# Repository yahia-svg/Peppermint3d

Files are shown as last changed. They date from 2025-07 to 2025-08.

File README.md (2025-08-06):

# Peppermint3d
This is my fully custom designed bed slinger. I tried to make it as structurally sound as possible, by using mostly metal components like the opengantry universal plate and a ridgid aluminum frame, whilst still being fairly simple so i'd be able to build it as a beginner
# Motivation
I made this project because I was completely new to designing 3d printers and I thought this would be a great first printer. Additionally, this would help me so much with developing other hardware projects because the 3d printing service that I use is slow and expensive.
# Design
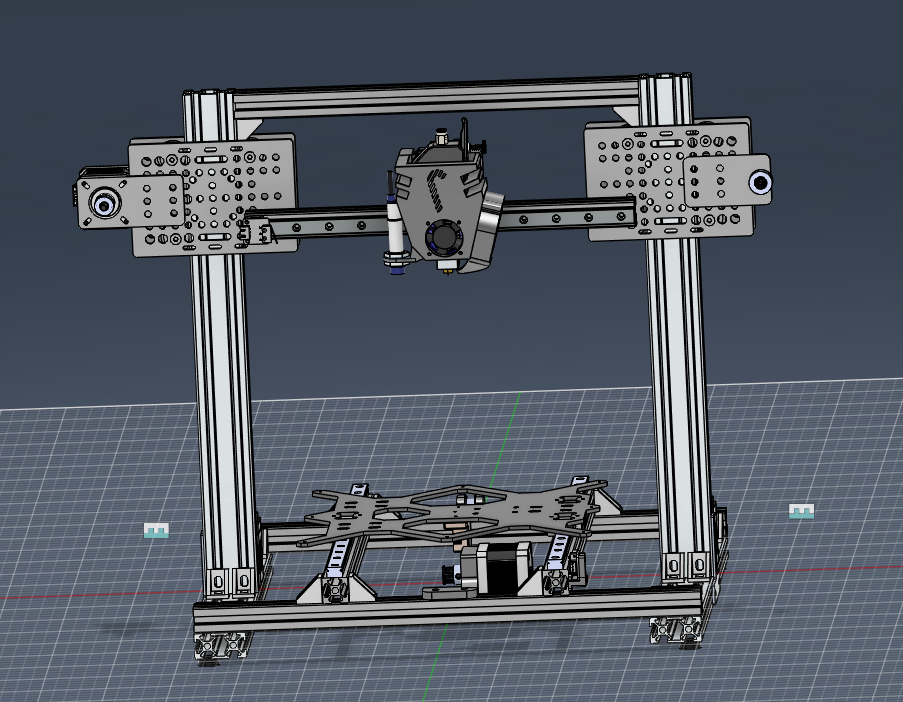
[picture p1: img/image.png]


# Video(Click to Play)
video (https://youtu.be/M26KKw5ZoOQ)

# BOM
| QUANTITY | NAME | COST | LINK | Notes |
|---|---|---|---|---|
| 1 | BIGTREETECH SKR MINI E3 V3.0 32 Bit Control Board | £3,300.00  | https://fluxelectronix.com/shop/bigtreetech-skr-mini-e3-v3-0-32-bit-control-board/ | |
| 1 | Proximity-Sensor | £140.00 | https://ampere-electronics.com/product/lj12a3-4-z-proximity-sensor-pnp-12mm-dia-4mm-3-wire-dc6-36v/ | |
| 1 | Raspberry Pi Zero 2 W | £0.00 | https://www.ram-e-shop.com/ar/shop/raspberry-pi-zero-2w-raspberry-pi-zero-2-w-9256 | will pay from terminal craft grant |
| 1 | ADXL345 Digital Accelerometer | £190.00 | https://ampere-electronics.com/product/gy-291-adxl345-accelerometer-module/ | |
| 1 | 5015 Blower fan -- 24v | £60.00 | https://fluxelectronix.com/shop/5015-blower-fan-12vdc/ | |
| 1 | E3d V6 Hotend full kit | £325.00 | https://fluxelectronix.com/shop/e3d-v6-j-head-hotend-1-75mm-extruder-nozzle-0-4mm/ | |
| 1 | Aluminium headted(214mm*214mm) 24v | £290.00 | https://fluxelectronix.com/shop/3d-printer-mk3-aluminum-heatbed-214x214x3mm-dual-supply/ | |
| 1 | Power Supply SMPS 240W 24V / 10A | £540.00 | https://fluxelectronix.com/shop/power-supply-smps-240w-24v-10a/ | |
| 1 | AC Inlet power socket with fuse holder | £15.00 | https://fluxelectronix.com/shop/panel-mount-ac-inlet-power-socket-with-fuse/ | |
| 1 | Power Supply cable | £35.00 | https://fluxelectronix.com/shop/ac-power-cord-with-iec-c13-connector/ | |
| 1 | zip ties | £25.00 | https://fluxelectronix.com/shop/200mm-nylon-cable-ties-pack-of-100-pcs-china/ | |
| 1 | NTC 100K ohm thermistor for heated bed | £30.00 | https://fluxelectronix.com/shop/100k-ohm-ntc-thermistors-temperature-sensor-with-cable-for-3d-printer-2pin-dupont-head/ | |
| 1 | Anti-vibration Rubber Feet, 4Pcs | £60.00 | https://fluxelectronix.com/shop/anti-vibration-rubber-feet-4pcs/ | |
| 4 | stepper Motor (NEMA-17) 17HS4401 | £1,600.00  | https://ampere-electronics.com/product/nema17-stepper-motor-17hs4401s-38mm/ | |
| 1 | Nema17 Stepper Motor 17HS4023 – 23mm | £315.00 | https://fluxelectronix.com/shop/nema17-stepper-motor-17hs4023-23mm/ | |
| 2 | Creality Ender-3/PRO Endstop Switch Module | £110.00 | https://fluxelectronix.com/shop/creality-ender-3-pro-endstop-switch-module/ | |
| 1 | Aluminium headted(214mm*214mm) 24v | £290.00 | https://fluxelectronix.com/shop/3d-printer-mk3-aluminum-heatbed-214x214x3mm-dual-supply/ | |
| 1 | PEI Sheet Double Side Textured Smooth 220x220mm | £900.00 | https://fluxelectronix.com/shop/pei-sheet-textured-smooth-220mm-twotrees/ | |
| 1 | bondtech bmg extruder kit | £475.00 | https://fluxelectronix.com/shop/flexible-consumables-double-gear-extruder-bondtech-bmg-reduced-extruder/ | |
| 1 | 32gb sd card for raspberry pi | £375.00 | https://www.ram-e-shop.com/ar/shop/micro-sd-32gb-krt-mymwry-mykrw-32-jyj-hc10-6298 | |
| 4 | Leveling Screw (M3*40) | £60.00 | https://fluxelectronix.com/shop/leveling-kit-m3-screw-spring-knob-for-3d-printer/ | |
| 1 | Heat Bed High Power MOSFET Module 25A | £160.00 | https://fluxelectronix.com/shop/heat-bed-high-power-mosfet-module-25a/ | |
| 1 | Electric Copper Wire (1.5mm, 16 AWG, 1 Meter) | £22.50 | https://ampere-electronics.com/product/electric-copper-wire-1-5mm-16-awg-1-meter-el-sewedy-electric/ | |
| 3 | AWG22 copper wire | £15.00 | https://fluxelectronix.com/shop/copper-wire-0-5mm-22awg-1meter-long/ | |
| 1 | Dupont Crimp Connector Kit – 310Pcs | £135.00 | https://fluxeelectronix.com/shop/dupont-crimp-connector-kit-310pcs/ | |
| 4 | openbuilds universal gantry plate | £660.00 | https://fluxelectronix.com/shop/steel-v-slot-universal-gantry-plate-openbuilds/ | |
| 1 | PRUSA Y-carriage Plate | £200.00 | https://fluxelectronix.com/shop/prusa-y-carriage-plate-for-214x214mm-heated-bed-plate-black-steel/ | |
| 2 | Steel Flat T-Joining Plate | £90.00 | https://fluxelectronix.com/shop/steel-flat-t-joining-plate/ | |
| 1 | Steel Nema17 Motor Mount Plate | £45.00 | https://fluxelectronix.com/shop/steel-nema17-motor-mount-plate-openbuilds/ | |
| 1 | Steel Idler Pulley Plate | £40.00 | https://fluxelectronix.com/shop/steel-idler-pulley-plate-openbuilds/ | |
| 2 | Anti-Backlash Nut Block | £140.00 | https://fluxelectronix.com/shop/tr8x8-anti-backlash-nut-block-for-acme-lead-screw/ | |
| 2 | TR8x8 Acme Lead Screw – 300mm | £190.00 | https://fluxelectronix.com/shop/tr8x8-acme-lead-screw-300mm/ | |
| 2 | 5x8MM Flexible Shaft Coupler | £90.00 | https://fluxelectronix.com/shop/5x8mm-flexible-shaft-coupler/ | |
| 2 | Flange Bearing F688ZZ | £50.00 | https://ampere-electronics.com/product/f688zz-miniature-flanged-ball-bearing-8x16x5mm/ | |
| 8 | v wheel | £360.00 | https://fluxelectronix.com/shop/delrin-v-wheel/ | |
| 2 | toothless idler pulley | £70.00 | https://fluxelectronix.com/shop/toothless-gt2-idler-pulley-5mm-bore/ | |
| 2 | 20Teeth GT2 Timing Belt Pulley, 6mm Width, 5mm Bore | £60.00 | https://fluxelectronix.com/shop/20teeth-gt2-timing-belt-pulley-5mm-bore/ | |
| 21 | Aluminum Profile Corner Bracket | £273.00 | https://ampere-electronics.com/product/2020-aluminum-profile-corner-bracket/ | |
| 2 | 1m gt2 6mm belt | £90.00 | https://ampere-electronics.com/product/gt2-open-belt-6mm-wide-pu-with-steel-core-1-meter-black/ | |
| 9 | 6mm m5 spacer | £45.00 | https://fluxelectronix.com/shop/aluminum-spacer-5-1x10x6mm/ | |
| 1 | 1 meter mgn12 linear rail | £1,300.00  | https://ampere-electronics.com/product/mgn12-linear-rail-guide-1000mm/ | I will cut it up into 350mm 300mm and 300mm |
| 4 | mgn12 linear rail carriage | £2,000.00  | https://fluxelectronix.com/shop/mgn12h-linear-bearing-block/ | |
| 2.5 | v slot aluminum extrusion 2020 | £462.00 | https://fluxelectronix.com/shop/2020-v-slot-aluminum-profile-extrusion-1m-black-anodized/ | |
| 2 | v slot aluminum extrusion 2040 | £600.00 | https://fluxelectronix.com/shop/2040-v-slot-aluminum-profile-extrusion-1m-black-anodized/ | |
| 1 | 10 pack m5 washer | £6.00 | https://fluxelectronix.com/shop/m5-flat-galvanized-steel-washer-pack-of-10/ | |
| 1 | 3d printing estimate(3egp per gram) | £480.00 | Printify3d | |
| 1 | delivery estimate | £300.00 | Delivery for Printify - Flux - Ampere | |
| 1 | Screws and T nuts | £0.00 | | Will buy from my own money because it won't fit in the grant |
| | TOTAL PRICE | £17,018.50 | | |
| | PRICE IN USD | £351.26 | | |

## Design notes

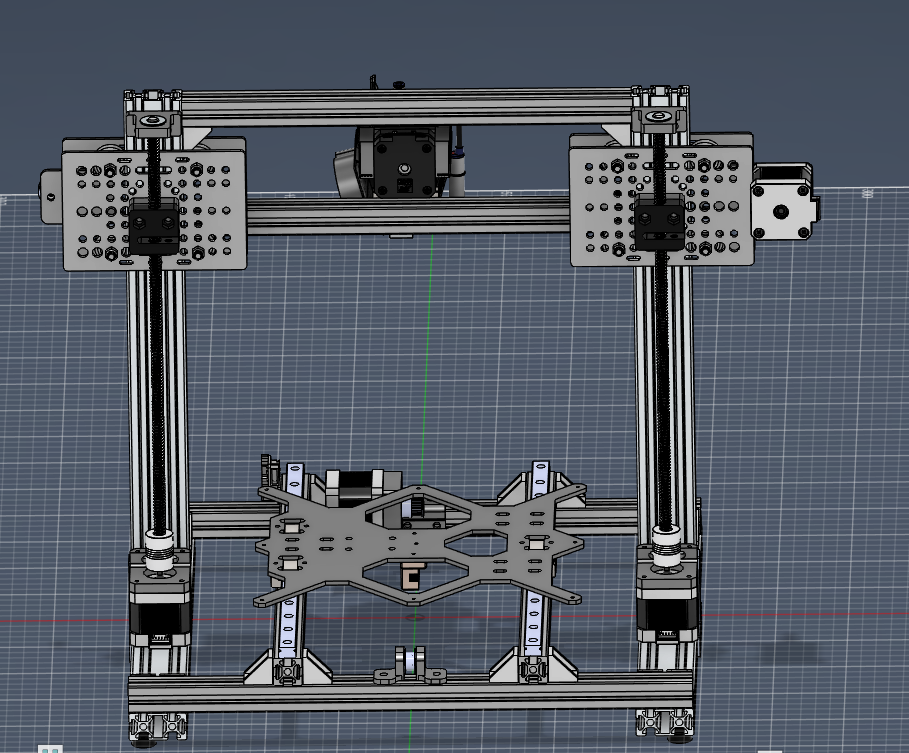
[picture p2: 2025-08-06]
img/Screenshot 2025-08-06 234610.png

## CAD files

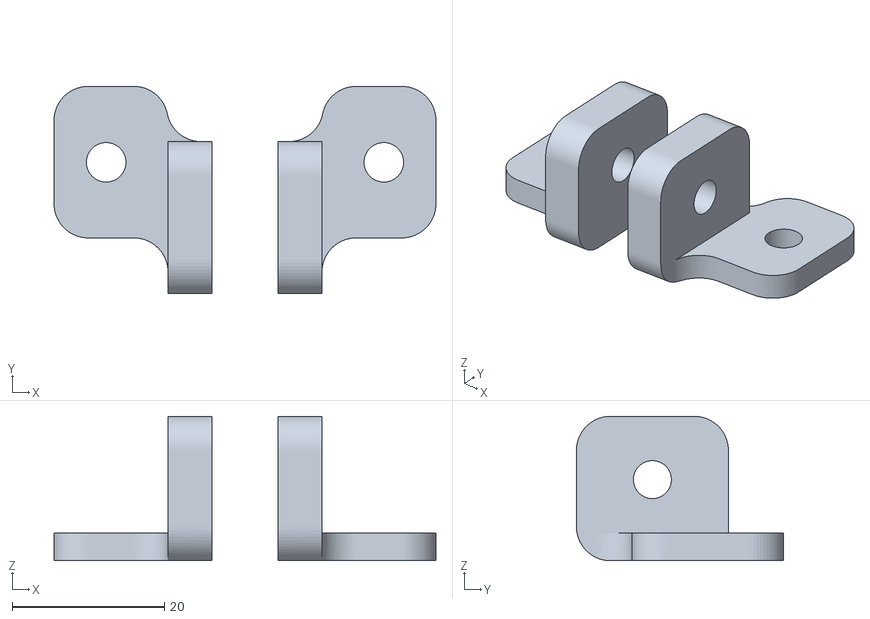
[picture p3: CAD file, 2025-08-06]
stl/idlerholder_y.stl
50.2 x 27.3 x 19.0

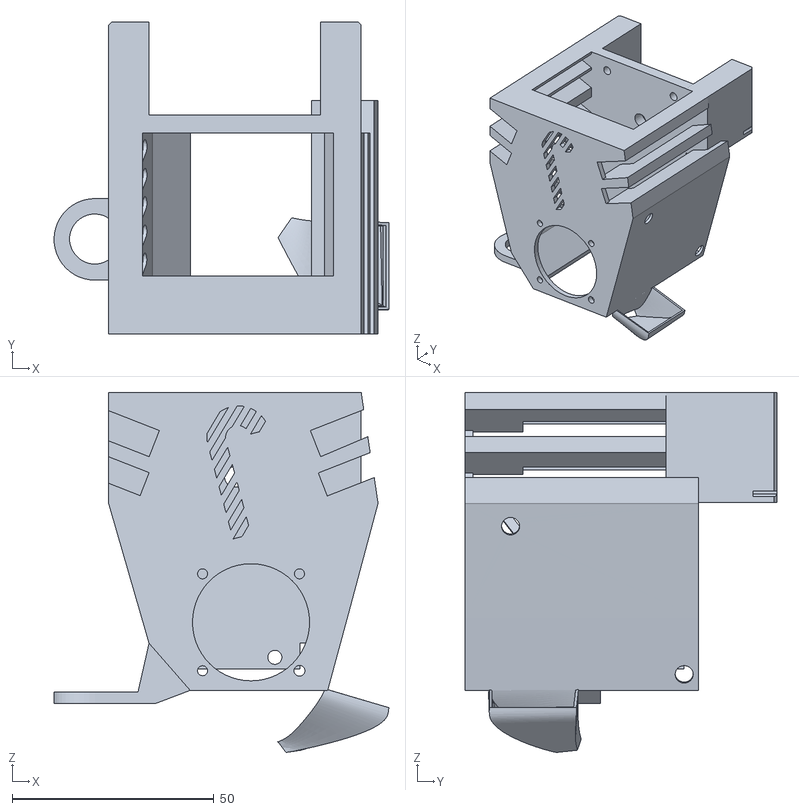
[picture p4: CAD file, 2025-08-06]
stl/printhead.stl
82.9 x 77.3 x 89.2

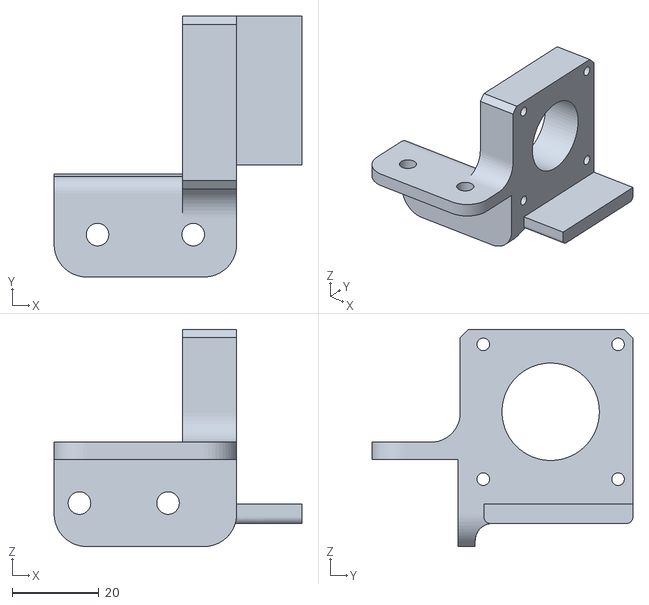
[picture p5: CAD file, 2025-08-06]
stl/motormount_y.stl
57.0 x 60.0 x 49.9

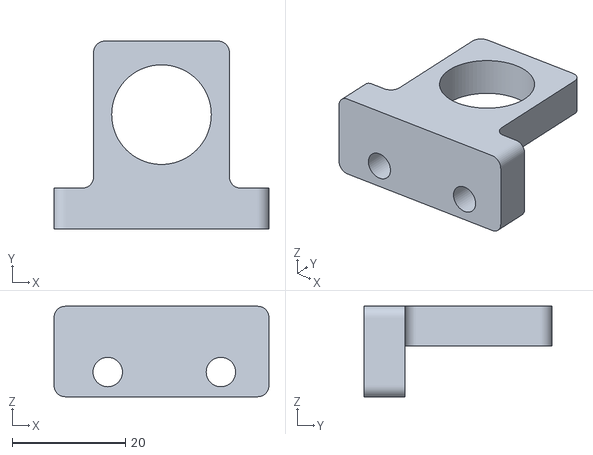
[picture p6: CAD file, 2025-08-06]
stl/bearingholder2_z .stl
38.0 x 33.2 x 16.0

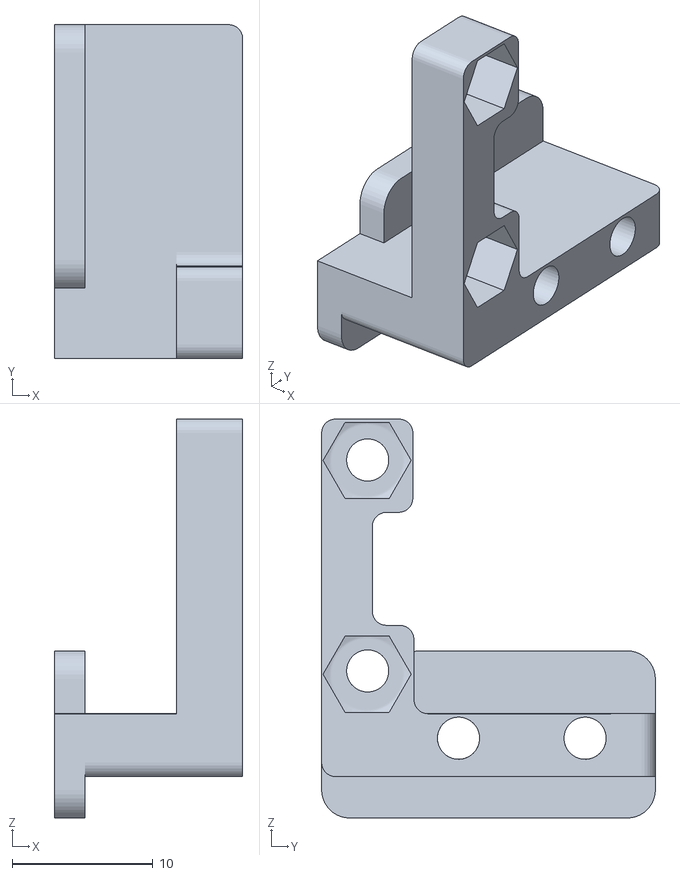
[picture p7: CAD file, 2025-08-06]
stl/endstop_y.stl
13.4 x 23.7 x 28.4

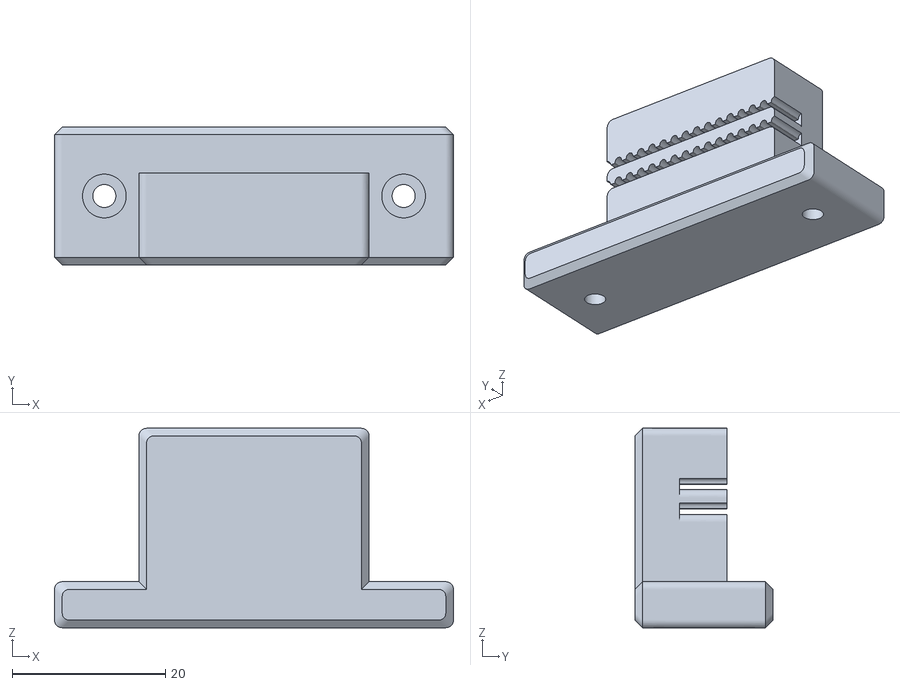
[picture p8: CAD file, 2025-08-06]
stl/MK3s_y_belt_holder_v1.0.stl
52.0 x 18.0 x 26.0

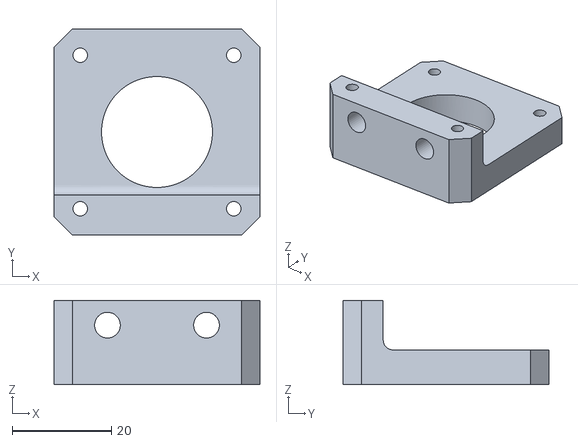
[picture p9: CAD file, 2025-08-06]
stl/motormount1_z.stl
41.6 x 41.6 x 17.0

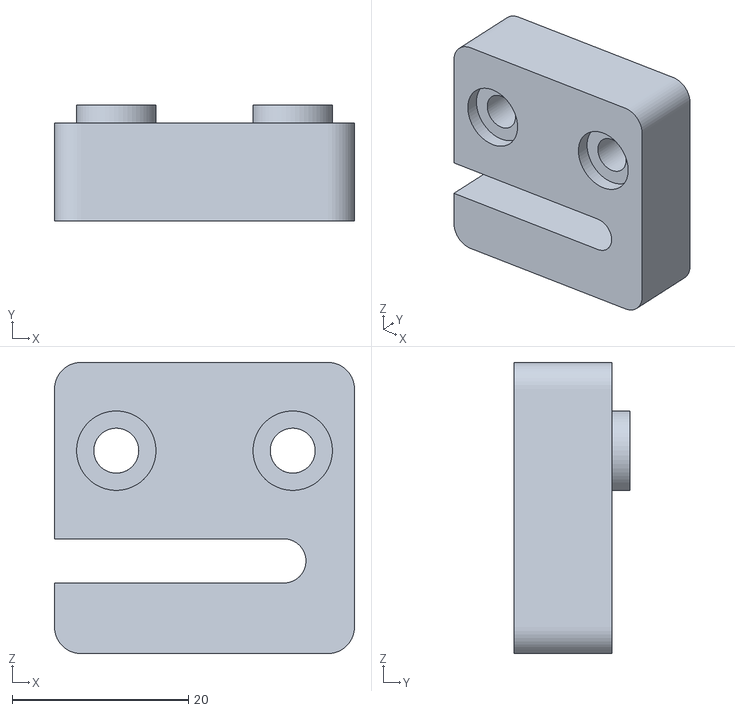
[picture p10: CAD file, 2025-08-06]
stl/antibacklashholder1_z.stl
34.0 x 13.1 x 33.0

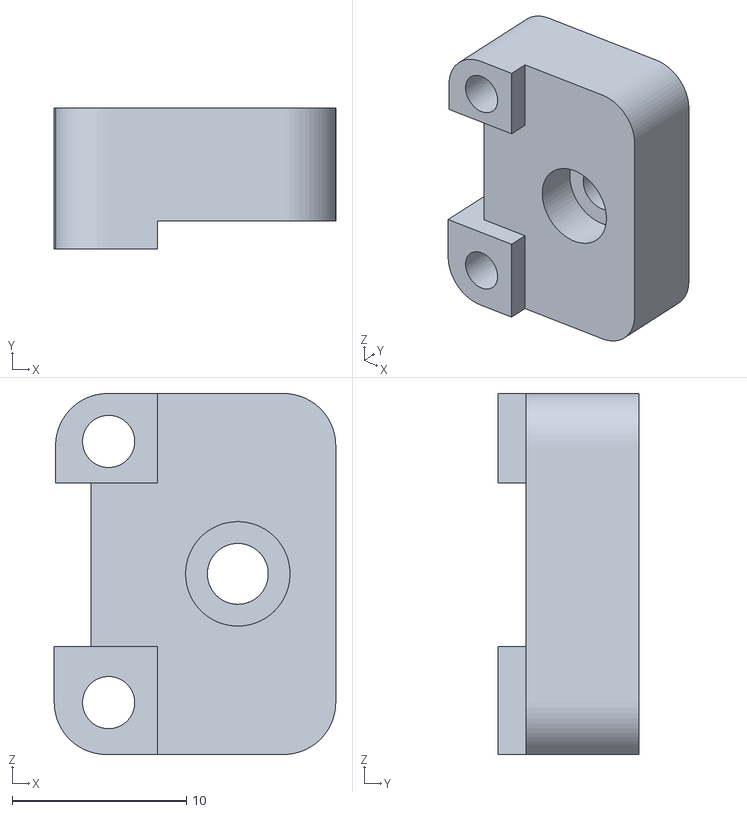
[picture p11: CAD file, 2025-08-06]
stl/endstop_x.stl
16.2 x 8.10 x 20.7

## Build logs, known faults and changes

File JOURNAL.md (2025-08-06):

## Total Hours: 19.5
| Key | Value |
|---|---|
| **Title** | Peppermint3d |
| **Author**  | Yahia Haggag |
| **Description** | My first custom bed slinger 3d printer designed to be sturdy and sleek |
| **Created At** | 2025-07-27 |

### 7/27/2025
As a complete noob to 3d printing and hardware I felt completely lost at first, so I started researching. I researched the different kinds of 3d printers and I finally settled on the bed slinger. I chose the bed slinger because it's a great choice for a first builds due to its simplicity and intuitive design. When choosing the specs for my printer I was focused on making it cheap and precise, therefore I've decided to use linear rails for the X and Y axis for precision and a lead screw actuator and v slot rails for the Z axis instead of linear rails to reduce costs. For the print head, I decided to use a direct drive bmg extruder to reduce stringing, and I coupled it with the e3d v6 volcano hotend, since it was really cheap and good enough for my needs, I also added a proximity sensor. For the print volume, I decided to go with 214*214*250 which is mostly sufficient for the things I print. To run this entire thing I decided to go with the BIGTREETECH SKR MINI E3 V3.0 board, because it's really cheap, really well docummented and runs klipper. I also estimated to cost to be 290USD based on local prices.
#### Time Elapsed: 7 Hrs 
### 7/28/2025
I hopped on fusion360 and got straight to designing I didn't do much as I was very unfimilliar with fusion but i managed to create a simple frame which I thought was strudy enough to support my 3d printer. I focused on strengthining my x axis by using 2040 extrusions and using a corner bracket and t plate combo because the x axis moves the most and it can be quite heavy
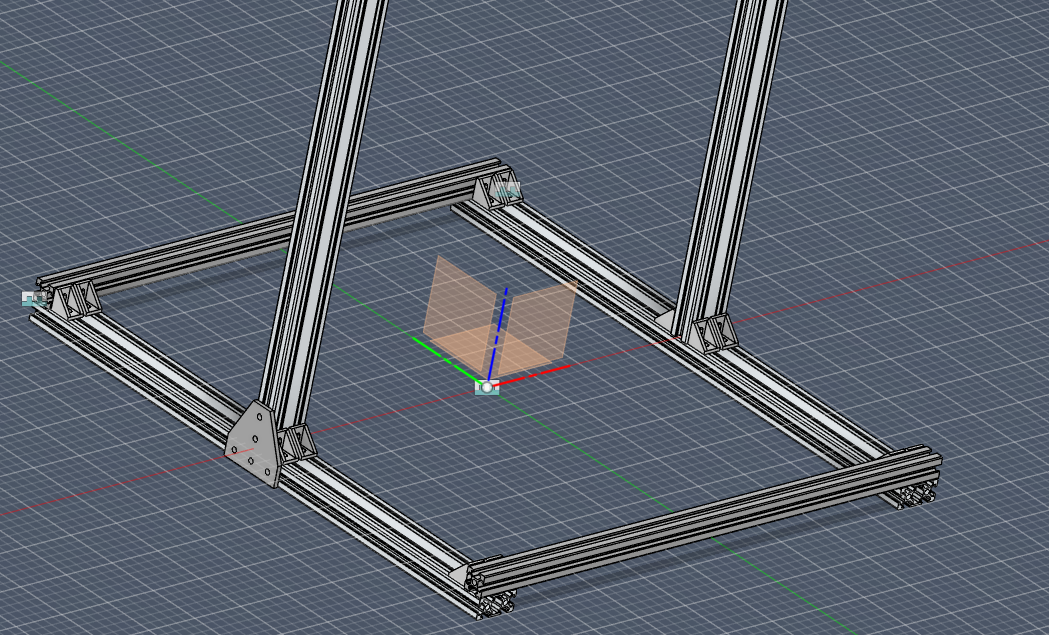
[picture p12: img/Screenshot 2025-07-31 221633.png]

#### Time Elapsed: 2 Hrs 
### 7/29/2025
I designed this endstop which is triggered by the linear rail carriage, this endstop helps me shorten the length of the linear rail as much as possible thus reducing cost. I also found out that the linear rail sizes I had initially calculated were incorrect, and now they're 350mm. I used the bed mount from the prusa mk3 since it was the only one available in my country that I could find the datasheet for online, and it also supports linear rails. So I had to use it since fabricating my own bed mount was going to be super expensive.
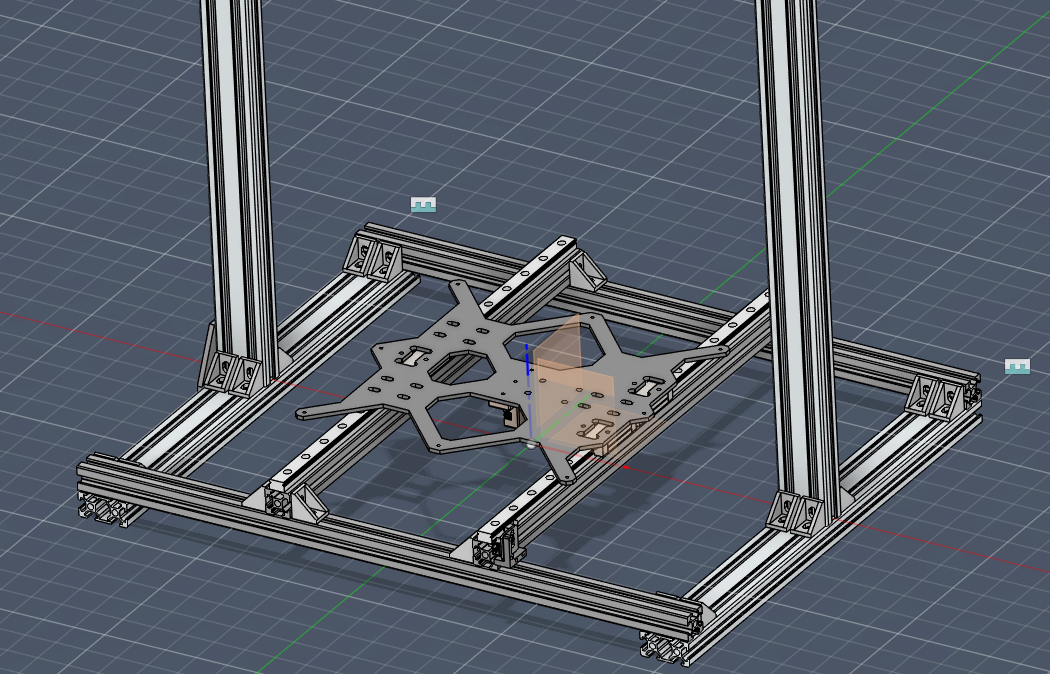
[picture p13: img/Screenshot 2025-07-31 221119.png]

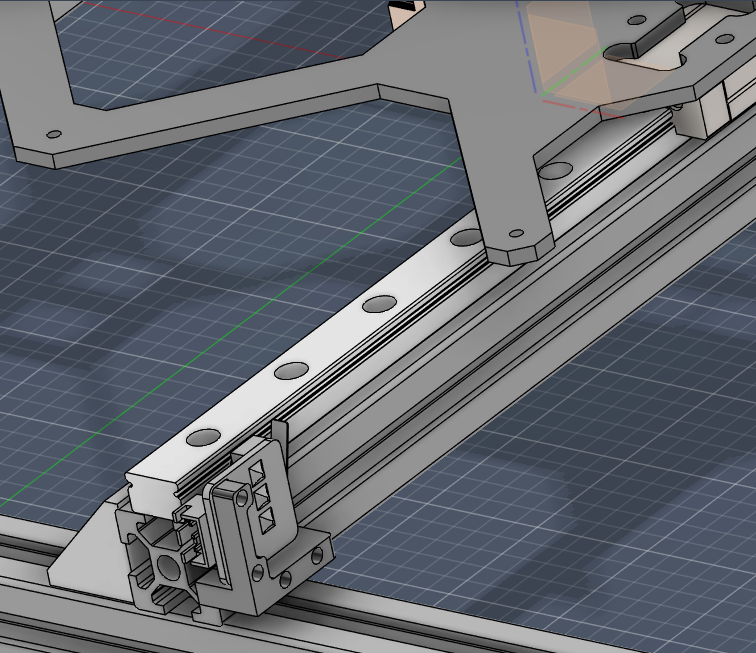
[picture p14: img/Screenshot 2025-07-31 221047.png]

#### Time Elapsed: 1.5 Hrs 
### 7/30/2025
Created a belt system for the y axis and added 4 anti vibration rubber feet
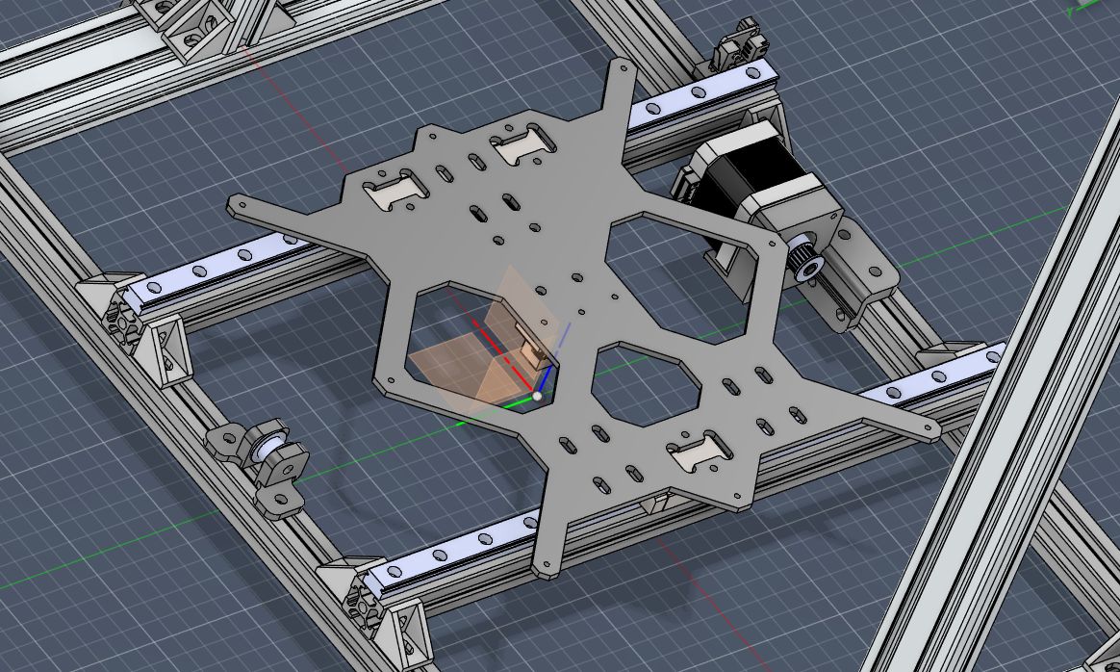
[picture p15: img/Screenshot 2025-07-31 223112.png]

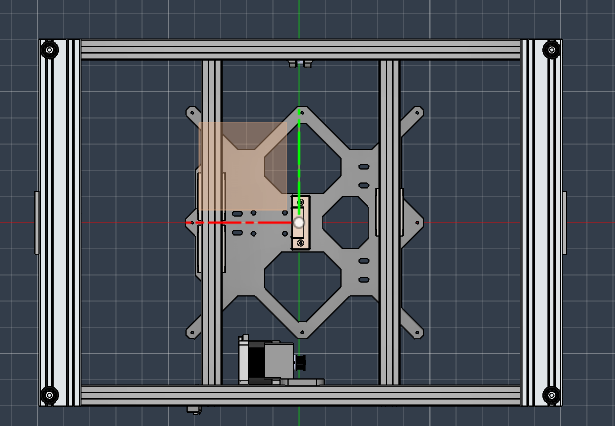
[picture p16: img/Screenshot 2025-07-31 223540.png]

#### Time Elapsed: 2 Hrs 
### 7/31/2025
I decided to lock in and I finished the entire z axis! I used openbuilds universal gantry plate because it's made of metal and has high surface area which means I can make the print head super heavy and I don't really have to worry.
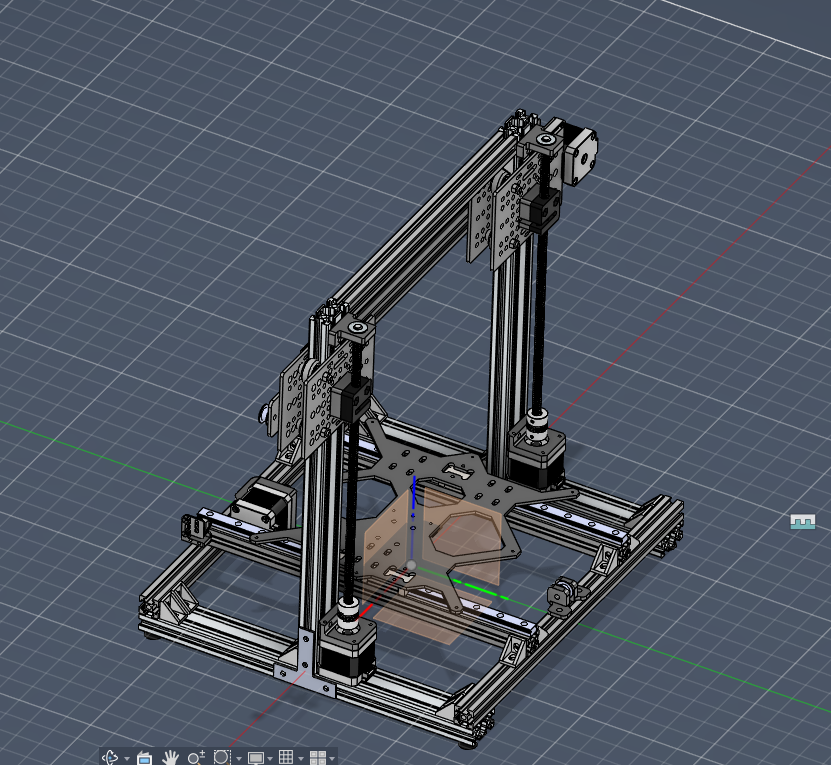
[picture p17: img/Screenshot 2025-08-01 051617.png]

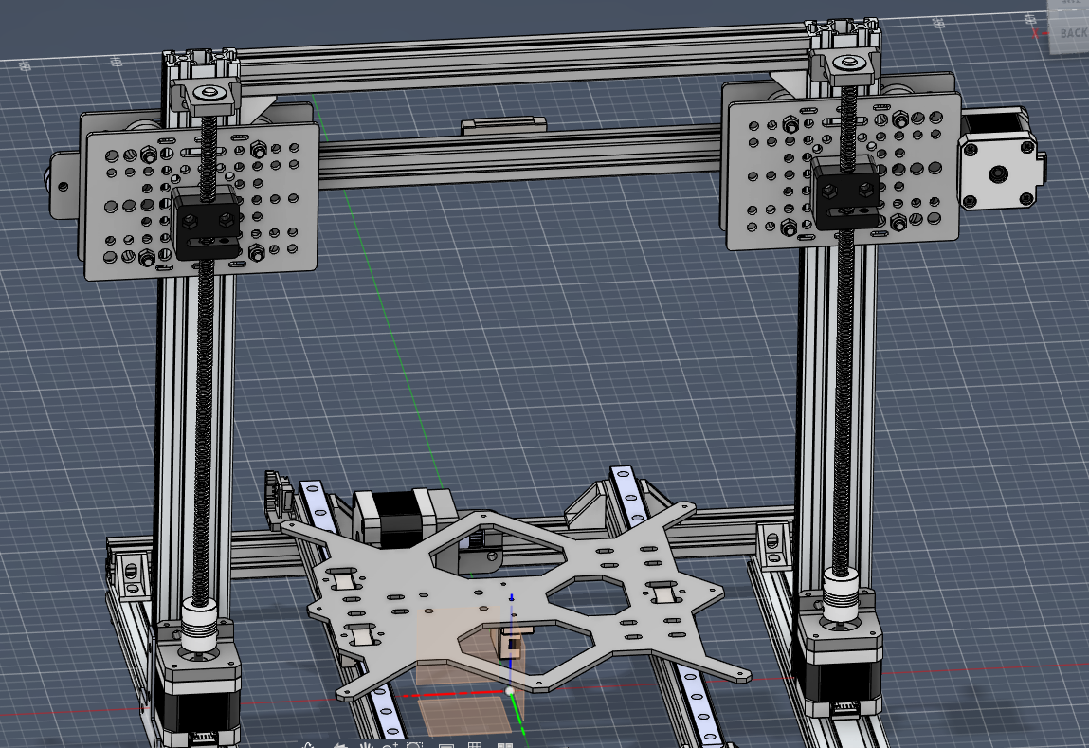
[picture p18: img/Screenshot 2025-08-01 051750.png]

#### Time Elapsed: 4 Hrs 
### 8/1/2025
Speedran the x axis and printhead because of the deadline
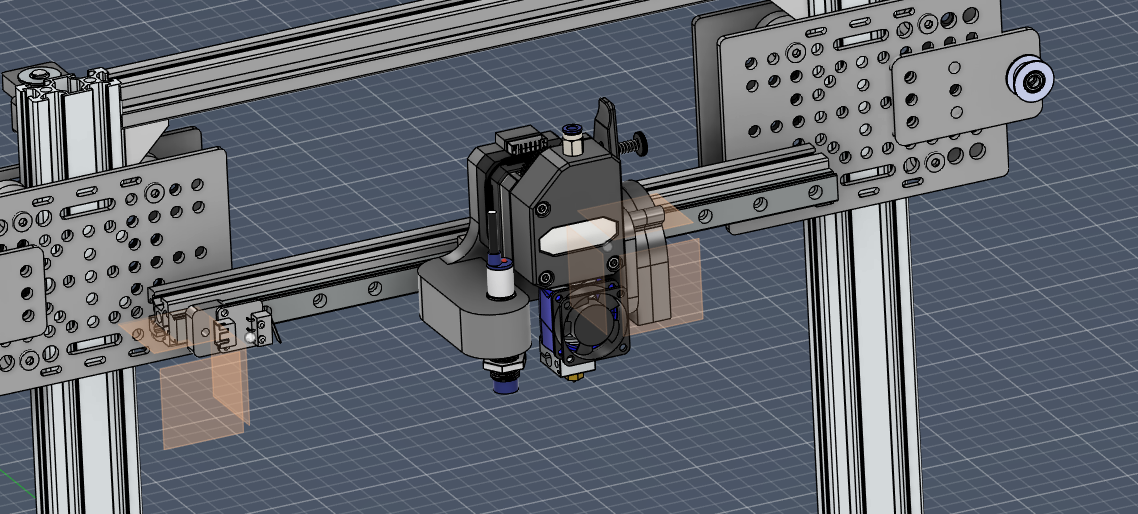
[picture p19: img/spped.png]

#### Time Elapsed: 3 Hrs 
### 8/5/2025
Completely revamped the design of the printhead and added a printhead cover after discovering a major flaw in how the printhead was assembeled.
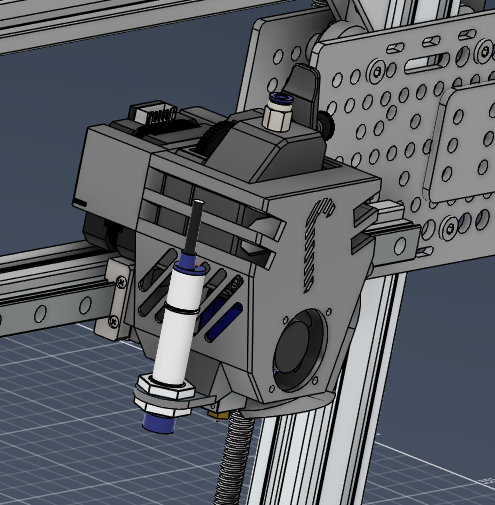
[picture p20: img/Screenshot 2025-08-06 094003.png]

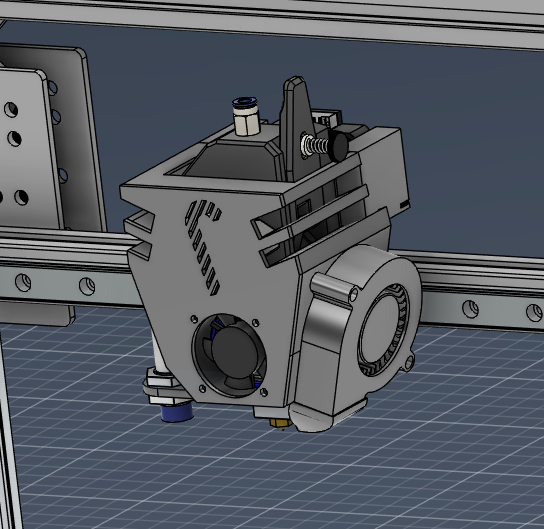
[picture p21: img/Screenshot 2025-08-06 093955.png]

#### Time Elapsed: 4 Hrs
